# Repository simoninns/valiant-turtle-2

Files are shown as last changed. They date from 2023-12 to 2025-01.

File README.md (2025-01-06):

# Valiant Turtle 2
The Valiant Turtle 2 is a modern re-creation of the Valiant Turtle robot from the 1980s.  The project is fully open-hardware and open-software and is designed to be 3D printed and constructed from widely available parts.

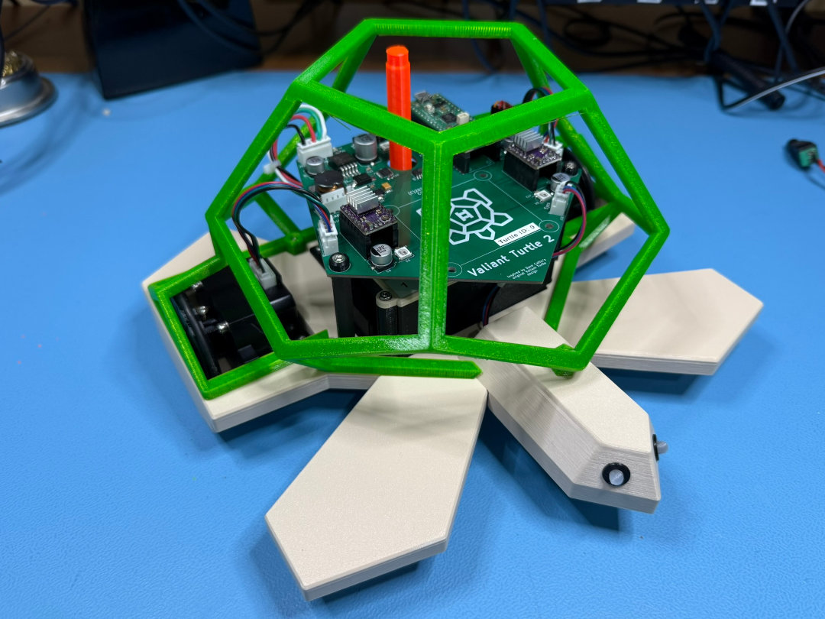
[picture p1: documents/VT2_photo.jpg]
Valiant Turtle 2


Please see the project Wiki for details of the project and for access to the project documentation.

## Project status
This project is at first release.  Please read the wiki and see YouTube for consruction videos (detailed in the wiki also).

## Author
Valiant Turtle 2 is designed and maintained by Simon Inns.

## Software License (GPLv3)

    Valiant Turtle 2 is free software: you can redistribute it and/or modify
    it under the terms of the GNU General Public License as published by
    the Free Software Foundation, either version 3 of the License, or
    (at your option) any later version.

    Valiant Turtle 2 is distributed in the hope that it will be useful,
    but WITHOUT ANY WARRANTY; without even the implied warranty of
    MERCHANTABILITY or FITNESS FOR A PARTICULAR PURPOSE.  See the
    GNU General Public License for more details.

    You should have received a copy of the GNU General Public License
    along with this program.  If not, see <http://www.gnu.org/licenses/>.

## Hardware License (Creative Commons BY-SA 4.0)
Please see the following link for details: https://creativecommons.org/licenses/by-sa/4.0/

You are free to:

Share - copy and redistribute the material in any medium or format
Adapt - remix, transform, and build upon the material
for any purpose, even commercially.

This license is acceptable for Free Cultural Works.

The licensor cannot revoke these freedoms as long as you follow the license terms.

Under the following terms:

Attribution - You must give appropriate credit, provide a link to the license, and indicate if changes were made. You may do so in any reasonable manner, but not in any way that suggests the licensor endorses you or your use.

ShareAlike - If you remix, transform, or build upon the material, you must distribute your contributions under the same license as the original.

No additional restrictions - You may not apply legal terms or technological measures that legally restrict others from doing anything the license permits.

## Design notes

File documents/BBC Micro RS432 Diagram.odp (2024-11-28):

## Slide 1

BBC Micro RS432 DTE

(Top)

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
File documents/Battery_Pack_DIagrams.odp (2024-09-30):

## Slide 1

18650

+

18650

+

18650

+

18650

+

BMS

B3

B2

B1

B+

B-

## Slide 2

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
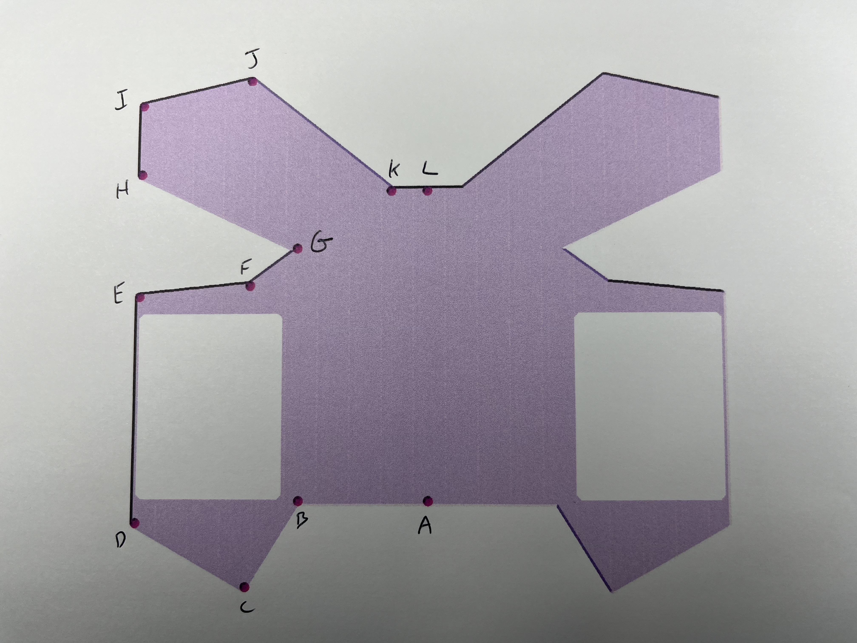
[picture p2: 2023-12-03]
openscad/robot/doc/body_points.jpg

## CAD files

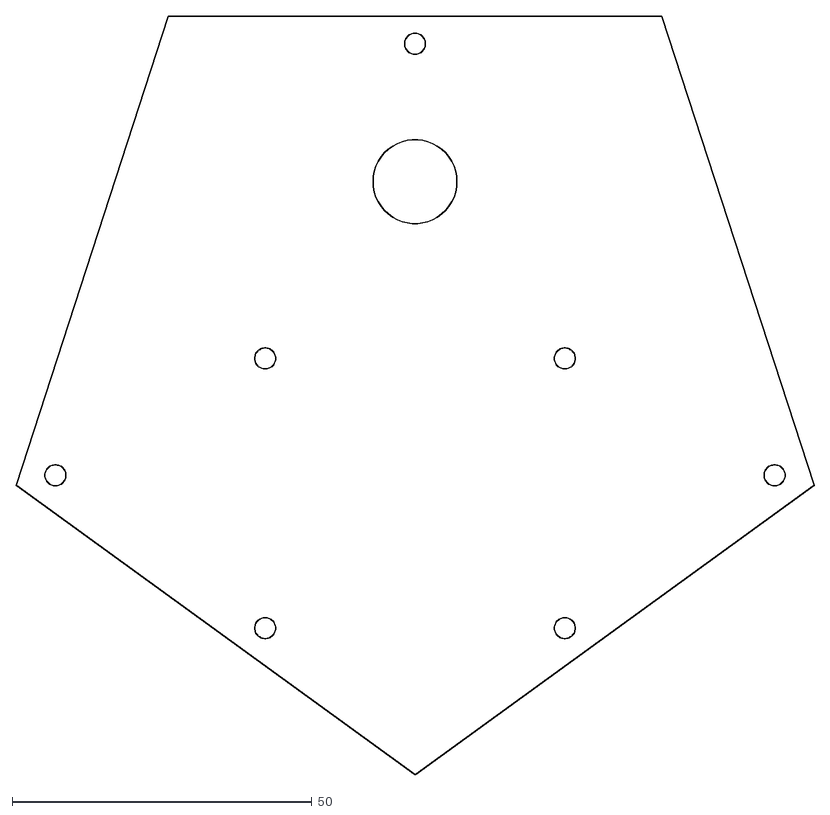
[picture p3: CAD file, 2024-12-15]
openscad/robot/dxf/main_pcb.dxf
133.1 x 126.6

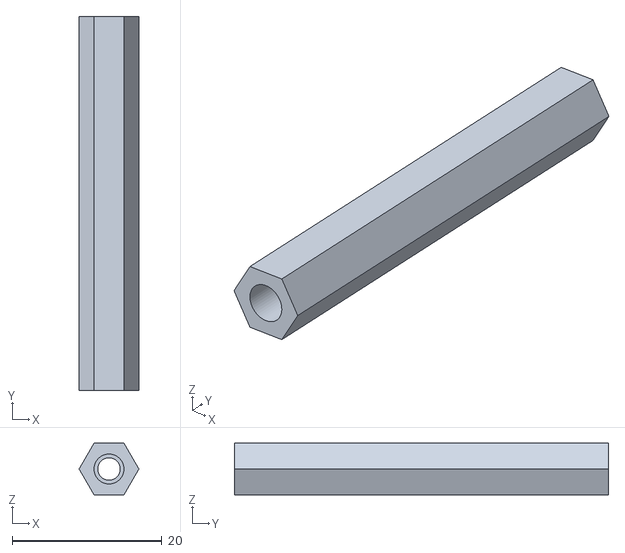
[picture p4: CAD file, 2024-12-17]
openscad/robot/stl/main_pcb_mounts_front.stl
8.00 x 50.0 x 6.93

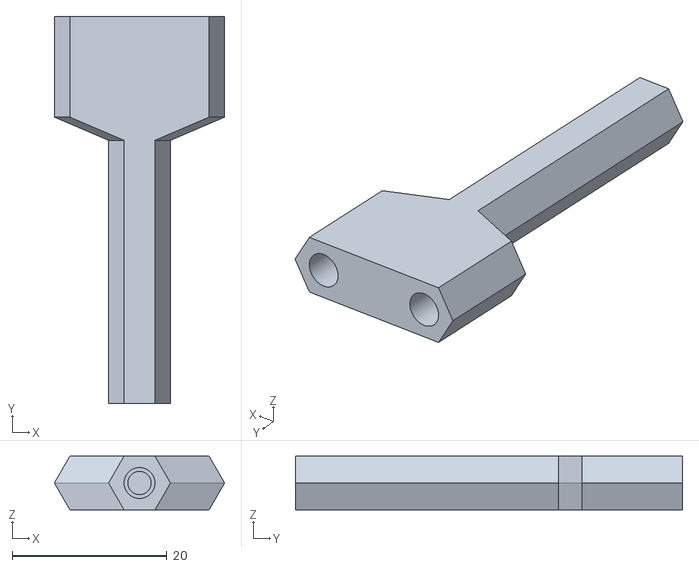
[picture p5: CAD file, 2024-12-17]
openscad/robot/stl/main_pcb_mounts_back.stl
22.0 x 50.0 x 6.93

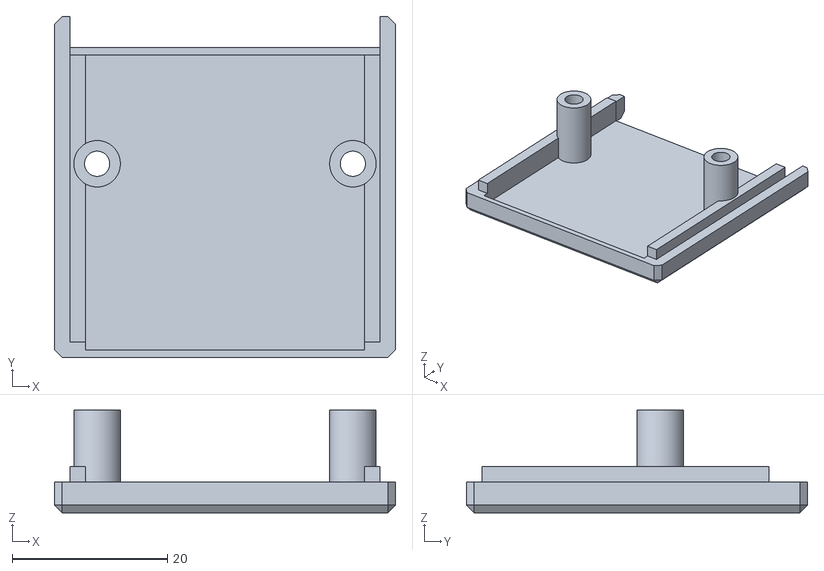
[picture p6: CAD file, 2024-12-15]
openscad/acorn_userport_adapter/stl/case_top.stl
44.0 x 44.0 x 13.2

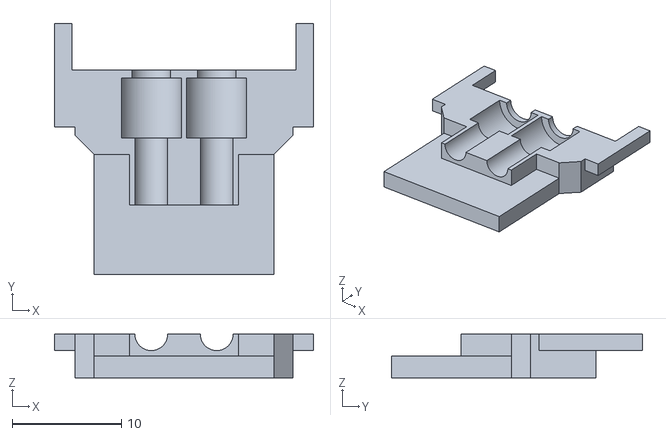
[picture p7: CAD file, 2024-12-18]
openscad/charger/stl/connector_front.stl
23.8 x 23.0 x 4.00

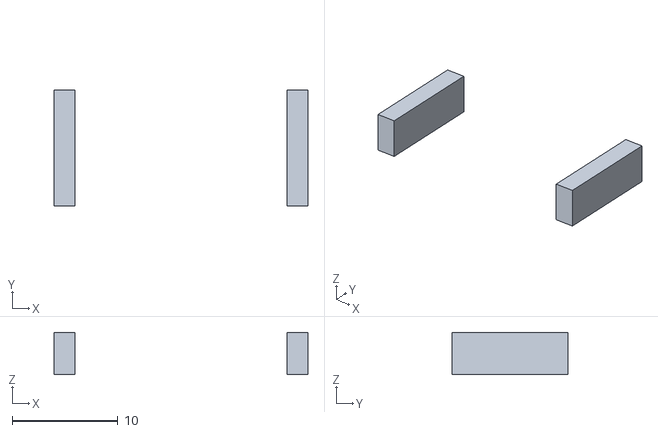
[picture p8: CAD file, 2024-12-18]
openscad/charger/stl_support_enforcers/connector_back_support_enforcer.stl
24.0 x 11.0 x 4.00

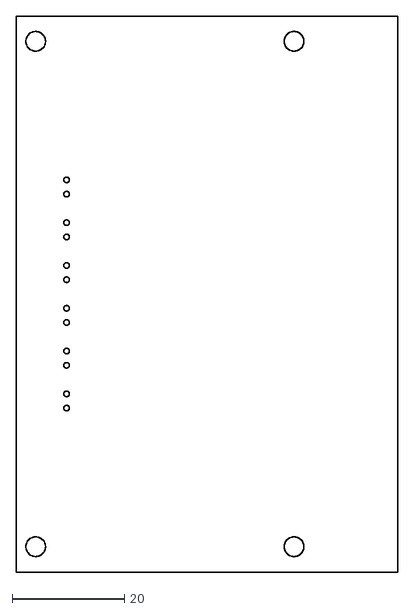
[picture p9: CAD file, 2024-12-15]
openscad/communicator/dxf/pcb.dxf
68.0 x 99.0

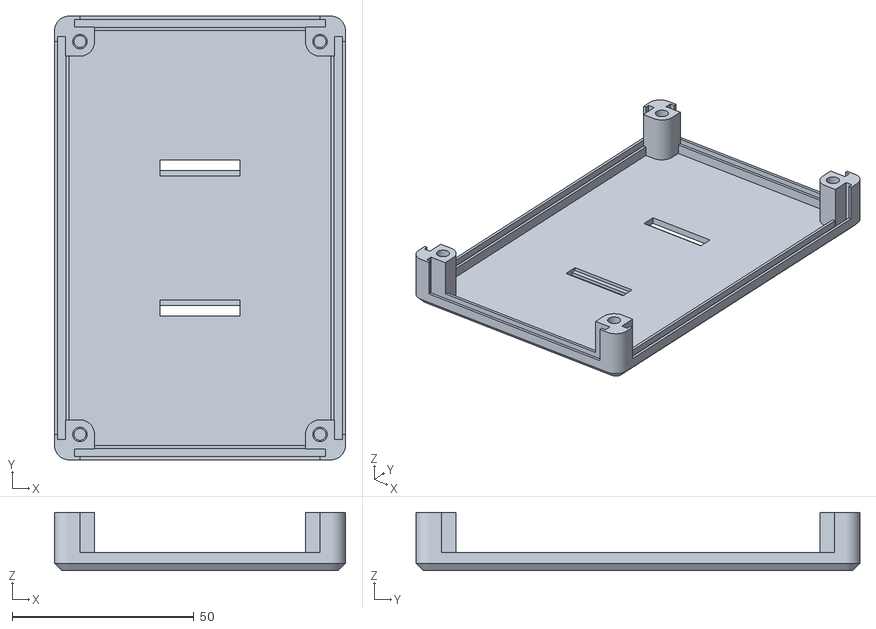
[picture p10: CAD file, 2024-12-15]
openscad/communicator/stl/case_top.stl
80.0 x 122.0 x 16.0

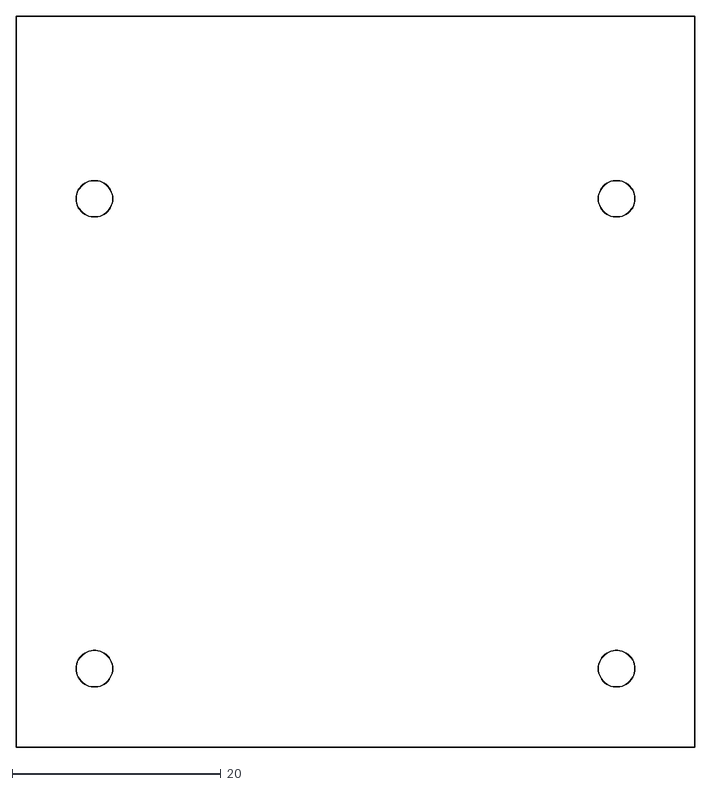
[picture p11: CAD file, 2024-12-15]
openscad/robot/dxf/aux_pcb.dxf
65.0 x 70.0

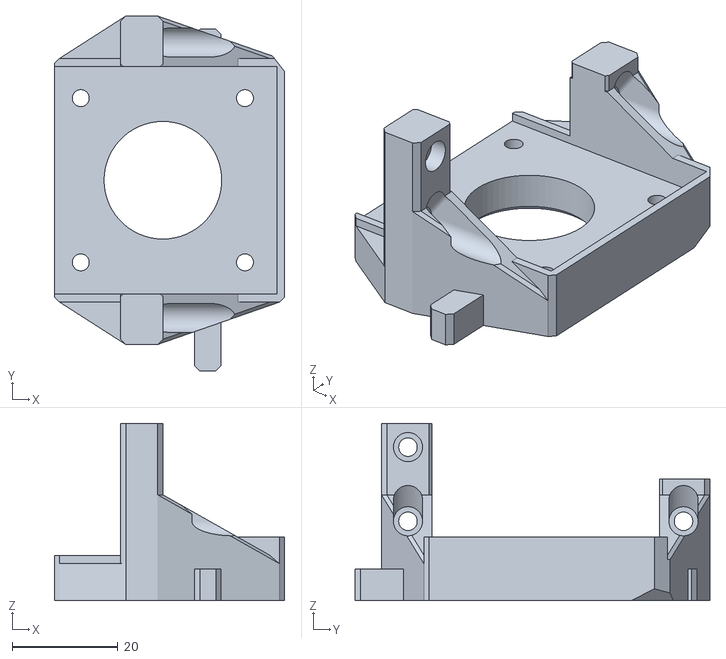
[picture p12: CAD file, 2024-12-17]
openscad/robot/stl/motor_mount_right.stl
43.5 x 67.0 x 33.5

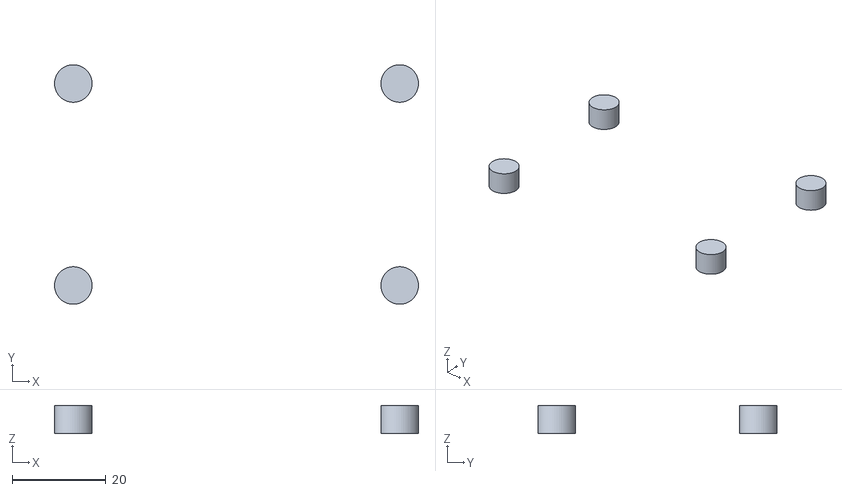
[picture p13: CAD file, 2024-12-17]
openscad/robot/stl_support_enforcers/body_right_support_enforcer.stl
77.5 x 51.0 x 6.00

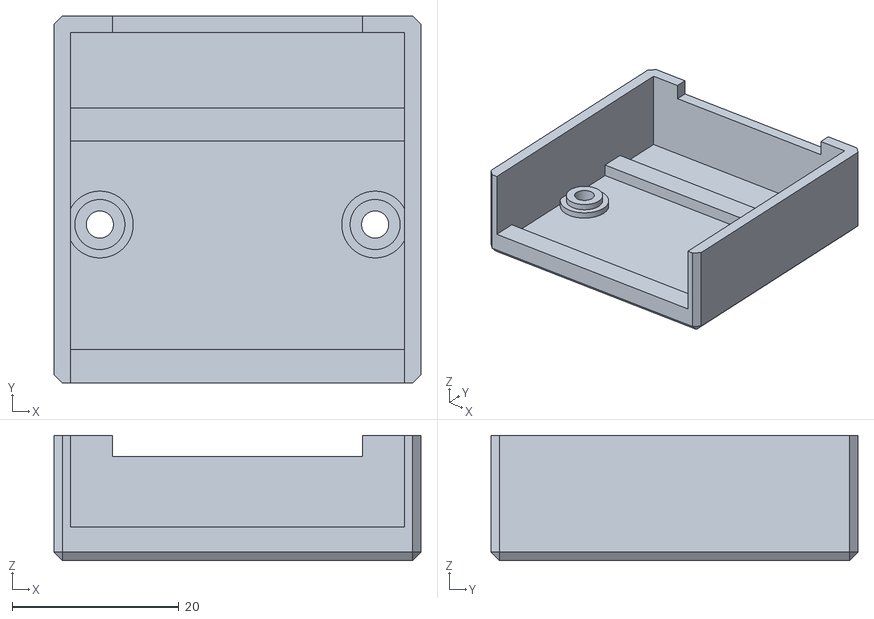
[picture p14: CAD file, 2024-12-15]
openscad/acorn_userport_adapter/stl/case_bottom.stl
44.0 x 44.0 x 15.0

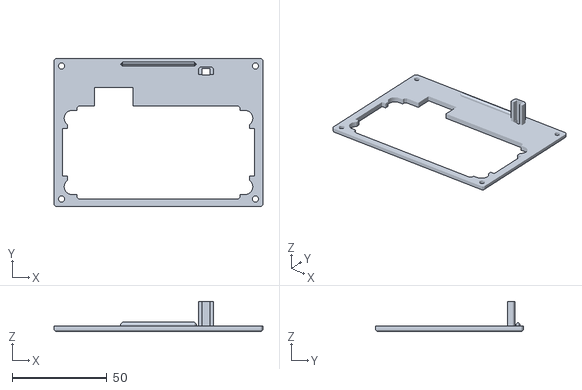
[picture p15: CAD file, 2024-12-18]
openscad/charger/stl/lid.stl
110.0 x 78.0 x 16.0

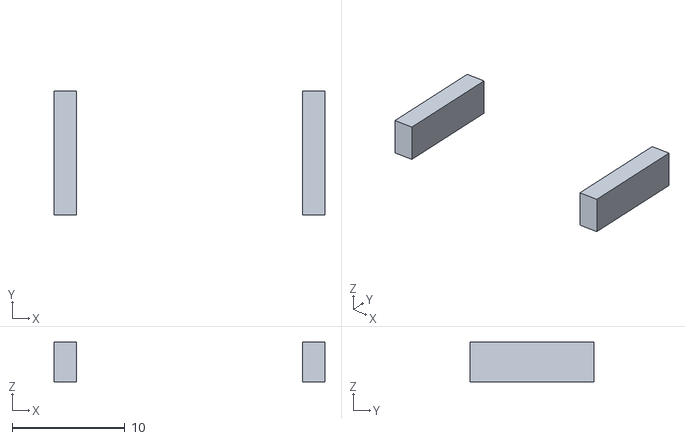
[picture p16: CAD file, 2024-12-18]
openscad/charger/stl_support_enforcers/connector_front_support_enforcer.stl
24.0 x 11.0 x 3.50

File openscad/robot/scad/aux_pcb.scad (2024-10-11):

/************************************************************************

    aux_pcb.scad
    
    Valiant Turtle 2
    Copyright (C) 2024 Simon Inns
    
    This is free software: you can redistribute it and/or modify
    it under the terms of the GNU General Public License as published by
    the Free Software Foundation, either version 3 of the License, or
    (at your option) any later version.
    
    This program is distributed in the hope that it will be useful,
    but WITHOUT ANY WARRANTY; without even the implied warranty of
    MERCHANTABILITY or FITNESS FOR A PARTICULAR PURPOSE.  See the
    GNU General Public License for more details.
    
    You should have received a copy of the GNU General Public License
    along with this program.  If not, see <http://www.gnu.org/licenses/>.
    
    Email: simon.inns@gmail.com
    
************************************************************************/

include <BOSL/constants.scad>
use <BOSL/transforms.scad>
use <BOSL/shapes.scad>

include <main_pcb.scad>

// Screw holes for the aux board
module aux_screws()
{
    move([0,0,0]) {
        move([+(50/2),+(45/2),0]) cyl(h=10, d=3.5);
        move([-(50/2),+(45/2),0]) cyl(h=10, d=3.5);
        move([+(50/2),-(45/2),0]) cyl(h=10, d=3.5);
        move([-(50/2),-(45/2),0]) cyl(h=10, d=3.5);
    }
}

// The aux PCB is to allow easy additions to the turtle without
// having to redesign the main control board.
module aux_pcb() 
{
    move([0,-23,1.5+20]) {
        difference() {
             color([0.0,0.6,0.0,1]) move([0,5,0]) cuboid([55+10,50+20,1.5]);
            aux_screws();
        }
    }
}

module aux_pcb_mount_pillar()
{
    difference() {
        // Pillar
        cyl(h=20, d=8, $fn=6);

        // Threaded insert slot
        move([0,0,14 - 6]) xrot(180) cyl(h=8,d=4);
        move([0,0,-14 + 6]) xrot(180) cyl(h=8,d=4);
        move([0,0,0]) xrot(180) cyl(h=28,d=3);
    }
}

module aux_pcb_mount()
{
    move([0,0,10.75]) {
        move([+(50/2),+(45/2),0]) aux_pcb_mount_pillar();
        move([-(50/2),+(45/2),0]) aux_pcb_mount_pillar();
        move([+(50/2),-(45/2),0]) aux_pcb_mount_pillar();
        move([-(50/2),-(45/2),0]) aux_pcb_mount_pillar();
    }
}

module aux_pcb_screw_washer()
{
    // Use the same part as the main PCB
    main_pcb_screw_washer();
}

module aux_pcb_screw_washers()
{
    move([0,0,0]) {
        move([+(50/2),+(45/2),0]) aux_pcb_screw_washer();
        move([-(50/2),+(45/2),0]) aux_pcb_screw_washer();
        move([+(50/2),-(45/2),0]) aux_pcb_screw_washer();
        move([-(50/2),-(45/2),0]) aux_pcb_screw_washer();
    }
}

module render_aux_pcb(toPrint)
{
    if (!toPrint) {
        difference() {
            move([0,0,50.75]) aux_pcb();
        }
    } else {
        // This will allow you to render and export a DXF file that
        // can be used as a KiCAD PCB outline...
        projection() {
            aux_pcb();
        }
    }
}

module render_aux_pcb_mount(toPrint)
{
    if (!toPrint) {
            move([0,-23,50.75]) color([0.2,0.2,0.2,1]) aux_pcb_mount();
    } else {
        move([0,0,10]) aux_pcb_mount_pillar();
    }
}

module render_aux_pcb_screw_washer(toPrint)
{
    if (!toPrint) {
        move([0,-23,50.75]) color([0.2,0.2,0.2,1]) {
            move([0,0,24.25]) aux_pcb_screw_washers();
            zflip() move([0,0,2.75]) aux_pcb_screw_washers();
        }
    }
}

module render_aux_pcb_screws(toPrint)
{
    if (!toPrint) {
        // Top screws
        move([0,-23,74.5]) {
            move([+(50/2),+(45/2),0]) m3x10_screw();
            move([-(50/2),+(45/2),0]) m3x10_screw();
            move([+(50/2),-(45/2),0]) m3x10_screw();
            move([-(50/2),-(45/2),0]) m3x10_screw();
        }

        // Bottom screws
        move([0,-23,48.5]) {
            move([+(50/2),+(45/2),0]) xrot(180) m3x10_screw();
            move([-(50/2),+(45/2),0]) xrot(180) m3x10_screw();
            move([+(50/2),-(45/2),0]) xrot(180) m3x10_screw();
            move([-(50/2),-(45/2),0]) xrot(180) m3x10_screw();
        }
    }
}

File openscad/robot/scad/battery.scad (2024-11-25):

/************************************************************************

    battery.scad
    
    Valiant Turtle 2
    Copyright (C) 2024 Simon Inns
    
    This is free software: you can redistribute it and/or modify
    it under the terms of the GNU General Public License as published by
    the Free Software Foundation, either version 3 of the License, or
    (at your option) any later version.
    
    This program is distributed in the hope that it will be useful,
    but WITHOUT ANY WARRANTY; without even the implied warranty of
    MERCHANTABILITY or FITNESS FOR A PARTICULAR PURPOSE.  See the
    GNU General Public License for more details.
    
    You should have received a copy of the GNU General Public License
    along with this program.  If not, see <http://www.gnu.org/licenses/>.
    
    Email: simon.inns@gmail.com
    
************************************************************************/

include <BOSL/constants.scad>
use <BOSL/transforms.scad>
use <BOSL/shapes.scad>

// Non-printable parts ------------------------------------------------------------------

module battery18650_protected()
{
    // 18650 Battery with protection circuit
    difference() {
        cyl(h=69, d=18.5);
        move([0,0,(69/2)]) cyl(h=0.5, d=13);
        move([0,0,-(69/2)]) cyl(h=0.5, d=13);
    }
    
    move([0,0,(69/2)+0.25]) cyl(h=1, d=5);
}

module battery18650()
{
    // 18650 Battery without protection circuit
    difference() {
        cyl(h=65, d=18.5);
        move([0,0,(65/2)]) cyl(h=0.5, d=13);
        move([0,0,-(65/2)]) cyl(h=0.5, d=13);
    }
    
    move([0,0,(65/2)+0.25]) cyl(h=1, d=5);
}

module batteries()
{
    move([0,-2,0]) {
        move([19,10.25,1]) battery18650();
        move([19,-10.25,-1]) xrot(180) battery18650();

        move([-5.5,10.25,-1]) xrot(180) battery18650();
        move([-5.5,-10.25,1]) battery18650();
    }
}

module bullet_4mm_female()
{
    move([0,0,12.25/2]) difference() {
        union() {
            move([0,0,0]) cyl(h=12.25, d=4.25);
            move([0,0,-4.5-0.125]) cyl(h=3, d=4.75);
            move([0,0,-2.5 - 0.125 + 0.75 - 0.125]) cyl(h=0.75, d=4.75);
        }

        move([0,0,9.5 - 6]) cyl(h=7, d=3.5);
        move([0,0,-9.5+4]) cyl(h=7, d=3.5);
    }
}

module bms_pcb()
{
    difference() {
        union() {
            color([0,0.6,0,1]) cuboid([34,34,1.25], fillet=5, edges=EDGES_Z_ALL);

            // Pads
            color([0.8,0.8,0.0,1]) move([0,0,1]) {
                move([0,-15.5,0]) {
                    move([-9,0,0]) cuboid([6,3,1]); // B1
                    move([0,0,0]) cuboid([6,3,1]);  // B2
                    move([+9,0,0]) cuboid([6,3,1]);  // B3
                }

                move([-15.5,0,0]) cuboid([3,6,1]); // B-
                move([+15.5,0,0]) cuboid([3,6,1]); // B+

                move([0,14,-0.25]) {
                    move([-1.5 - 1.5,0,0]) cuboid([3,6,0.5], fillet=1.5, edges=EDGES_Z_ALL); // B1
                    move([+1.5 + 1.5,0,0]) cuboid([3,6,0.5], fillet=1.5, edges=EDGES_Z_ALL);  // B3
                }
            }
        }

        // Wire holes
        move([0,14,0]) {
            move([-1.5 - 1.5,0,0]) cyl(h=4,d=1);
            move([+1.5 + 1.5,0,0]) cyl(h=4,d=1);
        }
    }
}

// BMS PCB mock-up
module battery_pack_bms_pcb()
{
    move([0,-12.5,-8.5-8]) yrot(180) bms_pcb();
}

// Printable parts ----------------------------------------------------------------------

module battery_pack_clip()
{
    move([41.5,0,-15]) { 
        difference() {
            union() {
                move([3.5,0,+2.5]) cuboid([9, 24,35]);
                move([-1,-12,20]) right_triangle([9, 24, 9]);

                // Tab
                move([8.5,0,-13]) cuboid([3,18,4], chamfer=1, edges=EDGES_Z_ALL+EDGES_RIGHT);

                // Clip
                move([8,-9,6]) {
                    difference() {
                        right_triangle([3, 18, 3]);
                        move([4,9,0]) cuboid([3.5,20,3]);
                    }
                }
            }

            move([-2,0,-2]) union() {
                move([3.5,0,+2.5]) cuboid([9, 18+2,37.1]);
                move([-1,-10,21]) right_triangle([9, 18+2, 9]);
            }

            // Cut-outs to form side protectors
            move([+4,-9.5,9]) cuboid([24, 1,50]);
            move([+4,+9.5,9]) cuboid([24, 1,50]);
        }
    }
}

module bullet_connector_female_mask()
{
    move([0,0,9]) cyl(h=9,d=4.5);
    move([0,0,-0.5]) cyl(h=1,d=4);
    move([0,0,2.25]) cyl(h=5,d=5.5);
}

module battery_pack_screw_columns()
{
    // Screw columns
    move([45.5,18,-4]) {
        difference() {
            hull() {
                cyl(h=52,d=8);
                move([-4,0,0]) cuboid([1,8,52]); 
            }

            // Threaded insert
            cyl(h=64,d=3.25);
            move([0,0,+(34 - 10)]) cyl(h=8,d=4);
            move([0,0,-(34 - 10)]) cyl(h=8,d=4);
        }
    }

    move([45.5,-18,-4]) {
        difference() {
            hull() {
                cyl(h=52,d=8);
                move([-4,0,0]) cuboid([1,8,52]); 
            }

            // Threaded insert
            cyl(h=64,d=3.25);
            move([0,0,+(34 - 10)]) cyl(h=8,d=4);
            move([0,0,-(34 - 10)]) cyl(h=8,d=4);
        }
    }

    move([-45.5,18,-4]) {
        difference() {
            hull() {
                cyl(h=52,d=8);
                move([+4,0,0]) cuboid([1,8,52]); 
            }

            // Threaded insert
            cyl(h=64,d=3.25);
            move([0,0,+(34 - 10)]) cyl(h=8,d=4);
            move([0,0,-(34 - 10)]) cyl(h=8,d=4);
        }
    }

    move([-45.5,-18,-4]) {
        difference() {
            hull() {
                cyl(h=52,d=8);
                move([+4,0,0]) cuboid([1,8,52]); 
            }

            // Threaded insert
            cyl(h=64,d=3.25);
            move([0,0,+(34 - 10)]) cyl(h=8,d=4);
            move([0,0,-(34 - 10)]) cyl(h=8,d=4);
        }
    }
}

module battery_pack()
{
    difference() {
        move([0,-12.5,10]) {
            difference() {
                union() {
                    cuboid([86-0.5,49-0.5,60 -16], chamfer=1, edges=EDGES_Z_ALL);
                    move([0,0,-21.5]) cuboid([88,49-0.5,17], chamfer=1, edges=EDGES_Z_ALL);

                    // Battery connector
                    move([-23.5,27,-20.5]) move([0,-0.5,2.25]) cuboid([14,5,23.5]);
                }
                cuboid([81,44,64], chamfer=1, edges=EDGES_Z_ALL);

                // Battery connector
                move([-23.5 - 3,29,-22 + 3]) bullet_connector_female_mask();
                move([-23.5 + 3,29,-22 + 3]) bullet_connector_female_mask();

                // Cable gap
                move([-23.5 - 3,25,-27 + 0]) cuboid([4,10,8]);
                move([-23.5 + 3,25,-27 + 0]) cuboid([4,10,8]);
                move([-23.5 - 3,29,-24.5 + 3]) cyl(h=4,d=4);
                move([-23.5 + 3,29,-24.5 + 3]) cyl(h=4,d=4);

                // Clip slots
                move([-33.5,0,-17.25]) { 
                    move([1,23,0]) cuboid([2.5,9,21.5]);
                    move([19,23,0]) cuboid([2.5,9,21.5]);

                    // Angle the top of the slots for better printing
                    move([1,23,10.75]) yrot(45) cuboid([1.75,9,1.75]);
                    move([19,23,10.75]) yrot(45) cuboid([1.75,9,1.75]);
                    move([0.25 + 0.125,21,10.75]) yrot(45) cuboid([2.75 - 0.125,4,2.75 - 0.125]);
                    move([19.25 + 0.25 + 0.125,21,10.75]) yrot(45) cuboid([2.75 - 0.125,4,2.75 - 0.125]);

                    // Clip recess
                    move([-0.5,22,0]) cuboid([2,2,21.5]);
                    move([20.5,22,0]) cuboid([2,2,21.5]);
                }

                // Lower screw clearance
                move([45.5,18,-(34 - 6)]) cyl(h=8,d=4);
                move([-45.5,18,-(34 - 6)]) cyl(h=8,d=4);
                move([45.5,-18,-(34 - 6)]) cyl(h=8,d=4);
                move([-45.5,-18,-(34 - 6)]) cyl(h=8,d=4);
            }

            // Clip base
            move([-23.5,28,-29]) cuboid([20,12,2]);

            battery_pack_clip();
            xflip() battery_pack_clip();

            battery_pack_screw_columns();
        }

        // Recess for cover lock
        move([-23.5,9.75,-4.5]) cuboid([18.25,2,14.5]);
    }
}

module battery_pack_supports()
{
    move([+50.5,-12.5,-7]) cuboid([6,18,26]);
    move([-50.5,-12.5,-7]) cuboid([6,18,26]);
}

module battery_pack_connector_cover()
{
    move([0,-10.5,-21.5+3]) {
        // Battery connector
        difference() {
            difference() {
                move([-23.5,27.25,11.25]) cuboid([18,9.5,17.5 + 4]);
                move([-23.5,26.75 - 4,10]) cuboid([20,8.5,25]);
            }
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

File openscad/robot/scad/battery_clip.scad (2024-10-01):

/************************************************************************

    battery_clip.scad
    
    Valiant Turtle 2
    Copyright (C) 2024 Simon Inns
    
    This is free software: you can redistribute it and/or modify
    it under the terms of the GNU General Public License as published by
    the Free Software Foundation, either version 3 of the License, or
    (at your option) any later version.
    
    This program is distributed in the hope that it will be useful,
    but WITHOUT ANY WARRANTY; without even the implied warranty of
    MERCHANTABILITY or FITNESS FOR A PARTICULAR PURPOSE.  See the
    GNU General Public License for more details.
    
    You should have received a copy of the GNU General Public License
    along with this program.  If not, see <http://www.gnu.org/licenses/>.
    
    Email: simon.inns@gmail.com
    
************************************************************************/

include <BOSL/constants.scad>
use <BOSL/transforms.scad>
use <BOSL/shapes.scad>

// Battery contact (basic shape)
module battery_contact()
{
    difference() {
        union() {
            // Main body round lower part
            difference() {
                cyl(h=0.3, d=18.5);
                move([0,18.5/2,0]) cuboid([18.5+1,18.5, 1]);
            }

            // Main box rectangular upper part
            move([0,0+7/2,0]) cuboid([18.5,7, 0.3]);

            // Clips
            move([(8.25 - 0.5),6 - 5,0 +0.6]) zrot(180) right_triangle(size=[2,2,1.5], orient=ORIENT_X, center=true);
            move([-(8.25 - 0.5),6 - 5,0 +0.6]) zrot(180) right_triangle(size=[2,2,1.5], orient=ORIENT_X, center=true);

            // Soldering tag
            move([0,-14,0]) cuboid([5,1, 0.3]);
            move([0,-13.75+0.1,-0.5]) cuboid([5,0.3, 1.25]);

            move([0,-16.75,-1.25]) cuboid([5,6.5, 0.3]);
            move([0,-3,-1.25]) cyl(h=0.3, d=5);
        }

        move([0,-3,-1.25]) cyl(h=2, d=2.25);
    }
}

module battery_contact_negative()
{
    difference() {
        battery_contact();
        move([0,-1,0]) cyl(h=1,d=3);
    }
    
    // Spring 12mm high, 6mm,
    move([0,-1,6]) cyl(h=12, d=6); 

}

module battery_contact_positive()
{
    difference() {
        battery_contact();
        move([0,-1,0]) cyl(h=1,d=10);
    }

    move([0,-1,0]) {
        difference() {
            hull() {
                move([0,0,2]) cyl(h=0.3, d=6);
                move([0,0,0]) cyl(h=0.3,d=10);
            }

            move([0,0,-0.3]) hull() {
                move([0,0,2]) cyl(h=0.3, d=6);
                move([0,0,0]) cyl(h=0.3,d=10);
            }
        }
    }
}


module battery_contact_mask()
{
    cuboid([19,16,0.5]);

    // Centre clearance
    move([0,1,-2]) cuboid([11.5,14,4]);

    // Back centre clearance
    move([0,-3,2]) cuboid([5.5,10,4]);
    move([0,2,2]) zrot(45) cuboid([4,4,4]);
    move([0,-6,2]) cuboid([5.5,14,2]);

    // Tab clearance
    move([0,-10,0]) cuboid([5.5,16,0.5]);

    // Fastening clip channels
    move([(8.25 - 0.5),0.75,-0.75]) cuboid([2.5,3,1.25]);
    move([-(8.25 - 0.5),0.75,-0.75]) cuboid([2.5,3,1.25]);

    move([(8.25 - 0.5),5,-0.5]) cuboid([2.5,6,0.75]);
    move([-(8.25 - 0.5),5,-0.5]) cuboid([2.5,6,0.75]);
}


// 18650 x2 Battery clip
module battery_clip_body()
{
    difference() {
        union() {
            move([0,0,3.5+3]) cuboid([43,76,13], chamfer=0.5);
            move([0,+36.25,7+4]) cuboid([43,3.5,12], chamfer=0.5);
            move([0,-36.25,7+4]) cuboid([43,3.5,12], chamfer=0.5);
        }

        // Battery recesses
        move([-10.25,0,8.5]) ycyl(h=69,d=19);
        move([+10.25,0,8.5]) ycyl(h=69,d=19);

        // Screw recesses
        move([0,-(55.5/2),7.5]) cyl(h=13,d1=8, d2=12);
        move([0,+(55.5/2),7.5]) cyl(h=13,d1=8, d2=12);

        // Screw holes
        move([0,-(55.5/2),0]) cyl(h=8,d=3.5);
        move([0,+(55.5/2),0]) cyl(h=8,d=3.5);

        // Positive markers
        move([17,38.25,8]) {
            cuboid([5,1,1]);
            cuboid([1,1,5]);
        }

        move([-17,-38.25,8]) {
            cuboid([5,1,1]);
            cuboid([1,1,5]);
        }

        // Negative markers
        move([-17,38.25,8]) {
            cuboid([5,1,1]);
        }

        move([+17,-38.25,8]) {
            cuboid([5,1,1]);
        }

        // Orientation tab
        move([-18.75 + 1.5,-38.25 + 2,0]) cyl(h=1.1,d1=3, d2=2);

        // Side cut-outs to help get the batteries in and out
        move([0,18,11]) cuboid([48,22,9], chamfer=2);
        move([0,-18,11]) cuboid([48,22,9], chamfer=2);

        // Wiring gully
        move([0,39.5,6.5]) cuboid([20,4,4], chamfer=1);
        move([0,-39.5,6.5]) cuboid([20,4,4], chamfer=1);
    }
}

module battery_clip()
{
    difference() {
        battery_clip_body();

        xrot(90) {
            move([10.25,9.01,36.25]) battery_contact_mask();
            move([-10.25,9.01,36.25]) battery_contact_mask();
        }

        xrot(90) {
            move([10.25,9.01,-36.25]) yrot(180) battery_contact_mask();
            move([-10.25,9.01,-36.25]) yrot(180) battery_contact_mask();
        }
    }
}

module battery_clips()
{
    move([-1,0,0]) {
        xrot(-90) zrot(180) {
            move([10.25,9,-36.25]) battery_contact_positive();
            move([-10.25,9,-36.25]) battery_contact_negative();
        }

        xrot(90) zrot(0) {
            move([10.25,9,-36.25]) battery_contact_positive();
            move([-10.25,9,-36.25]) battery_contact_negative();
        }
    }
}

module render_battery_clip(toPrint)
{
    if (!toPrint) {
        color([0.2, 0.2, 0.2]) move([0,-12.5,9]) {
            move([0,-2.5,0]) yrot(90) xrot(90) zrot(180) battery_clip();
            move([0,+2.5,0]) yrot(90) xrot(-90) zrot(180) battery_clip();
        }
    } else {
        battery_clip();
    }
}

module render_battery_clip_contacts(toPrint)
{
    if (!toPrint) {
        color([0.8, 0.8, 0.8]) move([0,-12.5,10]) {
            move([0,-2.5,0]) yrot(90) xrot(90) zrot(180) battery_clips();
            move([0,+2.5,0]) yrot(90) xrot(-90) zrot(180) battery_clips();
        }
    }
}

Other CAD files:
openscad/communicator/stl/case_base.stl
openscad/robot/stl/head.stl
openscad/robot/stl_support_enforcers/battery_pack_lower_cover_support_enforcer.stl
openscad/acorn_userport_adapter/stl/support_enforcer.stl
openscad/robot/scad/body.scad
openscad/acorn_userport_adapter/scad/case.scad
openscad/acorn_userport_adapter/scad/main.scad
openscad/charger/scad/base.scad
openscad/charger/scad/battery_cutout.scad
openscad/charger/scad/bullet_connector.scad
openscad/charger/scad/connector.scad
openscad/charger/scad/lid.scad
openscad/charger/scad/light_pipe.scad
openscad/charger/scad/main.scad
openscad/charger/scad/pcb.scad
openscad/charger/scad/screws.scad
openscad/charger/stl/base.stl
openscad/charger/stl/connector_back.stl
openscad/charger/stl/light_pipe.stl
openscad/charger/stl_support_enforcers/charger_lid_support_enforcers.stl
openscad/communicator/scad/case.scad
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

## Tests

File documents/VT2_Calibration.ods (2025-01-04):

Valiant Turtle 2 – Calibration calculations
Linear calibration:
 | Diameter | 55.53 | mm
 | Circumference | 174.452640053841 | mm
 | Expected distance | 200 | mm
 | Number of rotations | 1.1464429540205 | rotations
 | Error | 0 | mm
 |  | .
 | Observed distance | 200 | mm
 | Observed diameter | 55.53
 | Difference | 0 | mm
 | Calibration setting | 0 | um
Rotational calibration:
 | Wheel diameter (observed) | 55.53 | mm
 | Circumference | 174.452640053841 | mm
 | Axel distance | 224 | mm
 | Turning circumference | 703.716754404114 | mm
 | Expected degrees of rotation | 1800 | degrees
 | Expected distance | 3518.58377202057
 | Number of rotations | 20.1692778678192
 | Error | -14 | degrees | (negative if turn is short)
 | Observed degrees of rotation | 1814 | degrees
 | Observed axel distance | 222.271223814774 | mm
 | Difference | -1.72877618522591 | mm
 | Calibration setting | 1729 | um

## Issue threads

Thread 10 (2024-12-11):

Make a better shell design for the robot

simoninns, 2024-12-11:
The shell has a number of issues (not least being a little too hard-coded in openscad).

A design that allows for transparent materials, mounting additional modules on the shell and easier printing, should be considered.

simoninns, 2024-12-15:
Fixed

Closed 2024-12-15.

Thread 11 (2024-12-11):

Add calibration sheet as PDF

simoninns, 2024-12-11:
The calibration sheet is only available as an Inkscape SVG at the moment - a PDF would be more useful for most people

simoninns, 2024-12-19:
Fixed

Closed 2024-12-19.

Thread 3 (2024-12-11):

Include battery monitoring and management

simoninns, 2024-12-11:
Right now you can only read the INA260 values manually.  The robot should be monitoring power and performing some actions when the battery is low.

simoninns, 2025-01-04:
Fixed in latest commit

Closed 2025-01-04.

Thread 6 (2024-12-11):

Prevent the Pico's USB connector from powering the robot

simoninns, 2024-12-11:
If you connect a USB cable to the Pico, the robot's 5V circuitry is powered including the LEDs.  This should be prevented.

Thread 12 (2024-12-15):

Servo horn missing support enforcer

simoninns, 2024-12-15:
The robot servo horn is missing a support enforcer for the main screw recess

simoninns, 2024-12-15:
Fixed

Closed 2024-12-15.

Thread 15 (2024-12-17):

BOMs on the wiki are not updated

simoninns, 2024-12-17:
Update all the BoMs on the wiki according to the current KiCAD board designs

simoninns, 2025-01-06:
Updated mainboard PCB BoM

simoninns, 2025-01-06:
Updated communicator BoM

Closed 2025-01-06.

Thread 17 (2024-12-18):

Charger connector missing support enforcers

simoninns, 2024-12-18:
The front and back charger connector is missing support enforcers (should be the same as the connector on the robot)

simoninns, 2024-12-18:
Fixed

Closed 2024-12-18.

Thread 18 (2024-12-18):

Communicator IR window

simoninns, 2024-12-18:
Missing instruction on how to make this and the materials required.

simoninns, 2025-01-06:
Fixed

Closed 2025-01-06.

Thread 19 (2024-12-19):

Create a python 'turtle'-like module

simoninns, 2024-12-19:
Python has a class for turtle graphics - a similar API could be implemented for controlling the VT2 (as well as dealing with connection via BLE and multiple turtles).

simoninns, 2024-12-19:
This should support a Cartesian coordinate system as well tracking the x,y position of the turtle in millimetres.  Like logo, it could support setpos, setx, sety, +xpos, +ypos, +pos and 'towards' which will turn the turtle to face an x,y position.

simoninns, 2025-01-04:
Fixed in latest commit

Closed 2025-01-04.

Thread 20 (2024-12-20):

Add threaded inserts to the servo holder

simoninns, 2024-12-20:
The 9G pen servo is held in place with the screws that generally come with them - directly into the plastic part.

It would be better if M2 or M2.5 bolts were used with threaded inserts in the plastic parts.

simoninns, 2024-12-20:
I measured this and there simply isn't space to do this - the clearance to the side of the servo is too small

Closed 2024-12-20.

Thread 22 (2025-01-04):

Robot firmware should use micrometers internally not millimetres

simoninns, 2025-01-04:
Millimetre accuracy is not good enough.  Convert the robot firmware to use mm on the command interface, but only micrometers internally

simoninns, 2025-01-05:
Fixed in latest commit

Closed 2025-01-05.

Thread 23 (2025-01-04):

Pen holder through PCB

simoninns, 2025-01-04:
It might be possible to extend the pen-holder through the PCB (so you can tighten and loosen it from above).  If so, implement.

simoninns, 2025-01-05:
This would require a redesign of the PCB.  Right now the biggest pen diameter is around 12mm and the PCB aperture is 14mm, so there is no space to get the threading through.

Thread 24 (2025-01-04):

Acornsoft Logo extension SCREEN command implementation

simoninns, 2025-01-04:
The SCREEN command should be able to ignore VT2 errors in the case that the robot is disconnected from the communicator before the SCREEN command is issued.  You should be able to pop back to screen mode without problems even if the robot has been turned off.

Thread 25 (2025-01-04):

Circle control inaccurate in firmware

simoninns, 2025-01-04:
The circle firmware commands do not keep the wheels in sync, so the circle command has a tendency to draw curves towards the start and end of the movement (which causes a loss of tracking accuracy).

simoninns, 2025-01-05:
Found a bug in diffdrive where the axel distance calibration was not being correctly applied.  Also changed diffdrive from millimetres to micrometres.  Probably needs a little more attention though.

simoninns, 2025-01-05:
Fixed in latest commit

Closed 2025-01-05.

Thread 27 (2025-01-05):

Robot firmware motor status LEDs

simoninns, 2025-01-05:
When running calitest2 it looks like the motor status LEDs are not correctly showing the direction of the motors at all times.

simoninns, 2025-01-05:
Fixed

Closed 2025-01-05.

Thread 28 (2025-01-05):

Robot firmware: Diffdrive setposition

simoninns, 2025-01-05:
Since set position is making multiple moves the LEDs are not updating.

This is because diffdrive isn't async so whilst it is waiting for the stepper movement to complete in a while loop, the get motor status call isn't happening (as the async execution is paused until it returns).  Meaning only the final setheading is reflected in the LEDs

Not really a bug, but a bit annoying.

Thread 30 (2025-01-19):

Shell too large for Ender 3

drdpj, 2025-01-19:
Shell STL is too large to print sensibly on something at the smaller end of the print volume scale, like an Ender 3 (220x220x250).

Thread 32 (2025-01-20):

Eye surround tolerance

drdpj, 2025-01-20:
This is going to be subjective with printer - the current 0.1mm difference between light-pipe and eye surround is too tight for mine. Widening the diameter of the hole in the surround to 5.3mm works nicely (0.4mm difference) - perhaps parameterise this?

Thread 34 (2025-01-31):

Bullet Connectors

drdpj, 2025-01-31:
It'd be useful to have a link to some example that fit the model as it stands - I've acquired some that have the same dimensions as the diagram on the wiki, but they really don't fit (it doesn't give any indication of length etc, etc)

simoninns, 2025-01-31:
I've updated the wiki with photos of the actual connectors used and measurements.  Open another issue if the issue persists (stating what's still missing :) )

Closed 2025-01-31.

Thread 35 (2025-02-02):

Bullet connectors

simoninns, 2025-02-02:
It seems there is some variance in the length and shape of the bullet connectors.  To make the model easier to modify it would be good if the grooves that hold the connector in place are only on the 'clip' side (so you only have to reprint the clip if it's wrong).

Also the connector itself should be made parametric to make modifying it easier.

Any examples of other 'shapes' would be useful.

drdpj, 2025-02-02:
https://www.amazon.co.uk/dp/B081TXM3XN

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

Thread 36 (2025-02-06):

Total number of screws and threaded inserts missing from wiki

simoninns, 2025-02-06:
As per the header, count them up and add them to the BoM (it's around 50)

simoninns, 2025-02-06:
It might be possible to use the CAD model to count and report the number required?

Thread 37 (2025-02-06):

Getting started instructions

drdpj, 2025-02-06:
Some instructions about how to load the firmware would probably be useful for many - I've never used micropython before, I used Thonny to upload it to the pico after a bit of googling.

Worth explaining that it connects via bluetooth, and you can do this directly from your PC without the communicator or anything. You don't have to add it as a device, the command line software will handle that.

To run the command line software you need the "bleak" bluetooth library installed. On windows it's just a "pip install bleak".

This should all go in before getting to the calibration.

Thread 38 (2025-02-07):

get_linear_velocity crashes firmware

drdpj, 2025-02-07:
Log output:

[INFO] CommandsRx::get_linear_velocity - Getting linear velocity
Traceback (most recent call last):
  File "<stdin>", line 139, in <module>
  File "main.py", line 203, in <module>
  File "main.py", line 201, in main
  File "asyncio/core.py", line 1, in run
  File "asyncio/core.py", line 1, in run_until_complete
  File "asyncio/core.py", line 1, in run_until_complete
  File "main.py", line 156, in aio_main
  File "asyncio/funcs.py", line 1, in gather
  File "asyncio/core.py", line 1, in run_until_complete
  File "control.py", line 266, in run
TypeError: can't convert float to int

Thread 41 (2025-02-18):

PCB enhancements

simoninns, 2025-02-18:
I was thinking about this a bit and wondering how (if I ever did another version) I would solve the PCB issue...  My conclusion is two-fold... Firstly I would make the PCB rectangular to drop the cost and size down and then I would mount the PCB in a printed pentagon to make it look 'right'.  This would also mean more flexibility around the pen mounting.  Once the board is smaller and cheaper, you could then use PCBA and get someone like JLCPCB to assemble it as well.

Also affects issue #23

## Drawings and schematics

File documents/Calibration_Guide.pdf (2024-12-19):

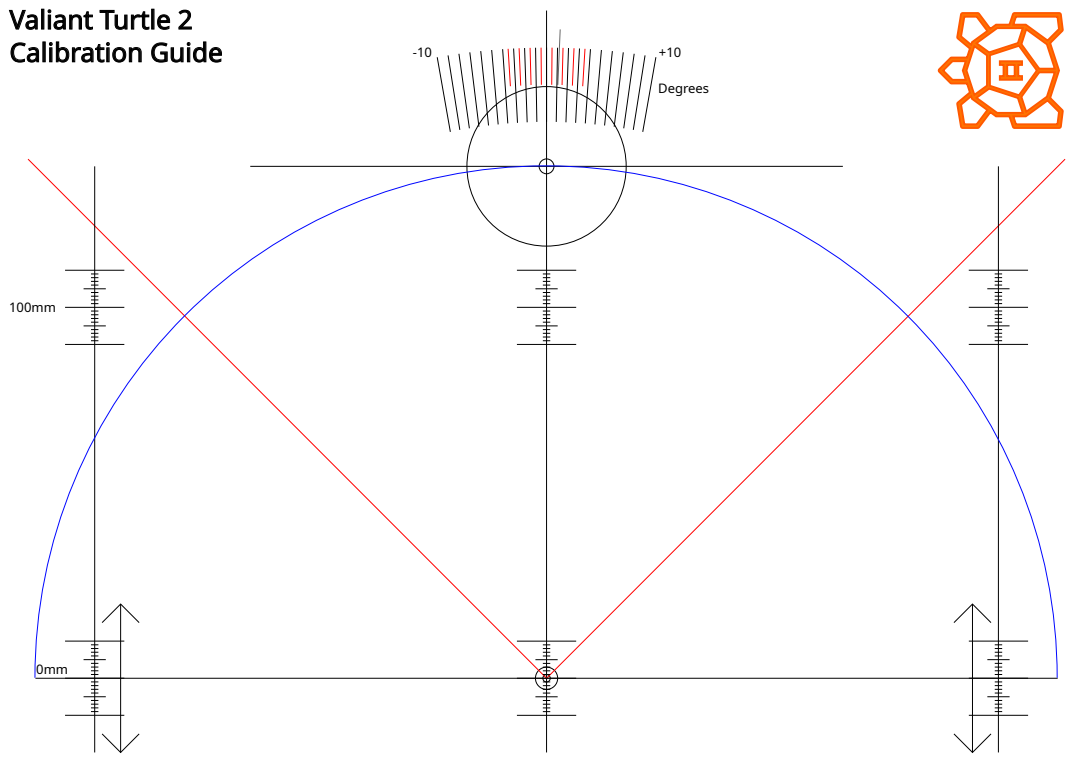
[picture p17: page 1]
Valiant Turtle 2 Calibration Guide; Degrees

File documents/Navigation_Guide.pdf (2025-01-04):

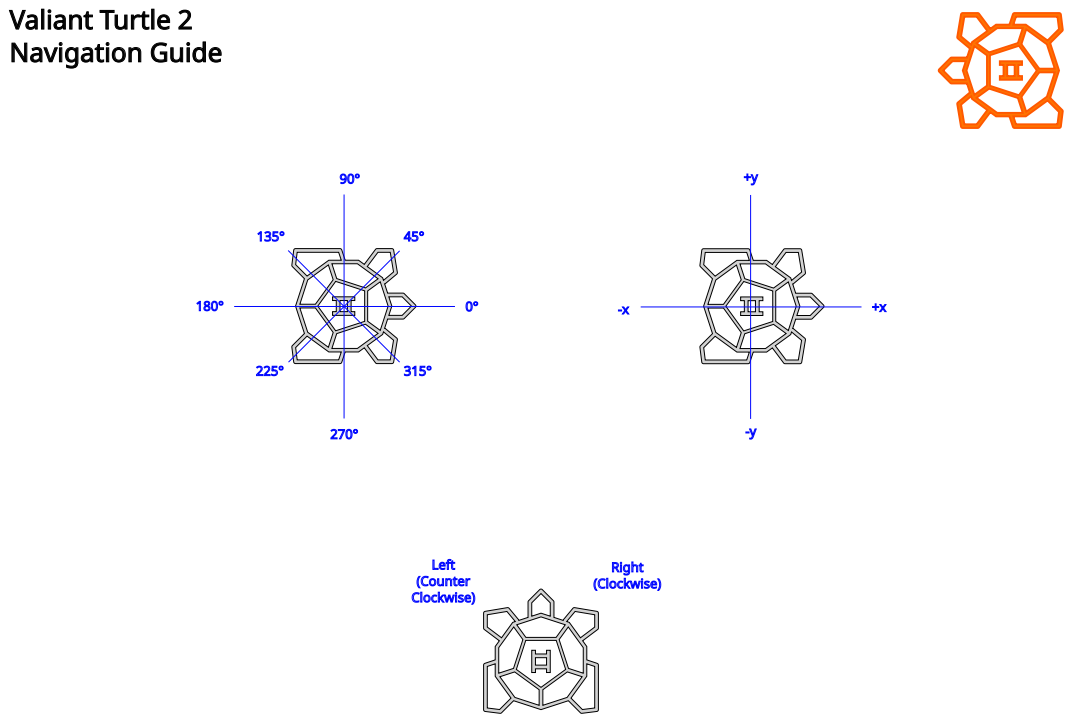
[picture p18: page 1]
Valiant Turtle 2 Navigation Guide

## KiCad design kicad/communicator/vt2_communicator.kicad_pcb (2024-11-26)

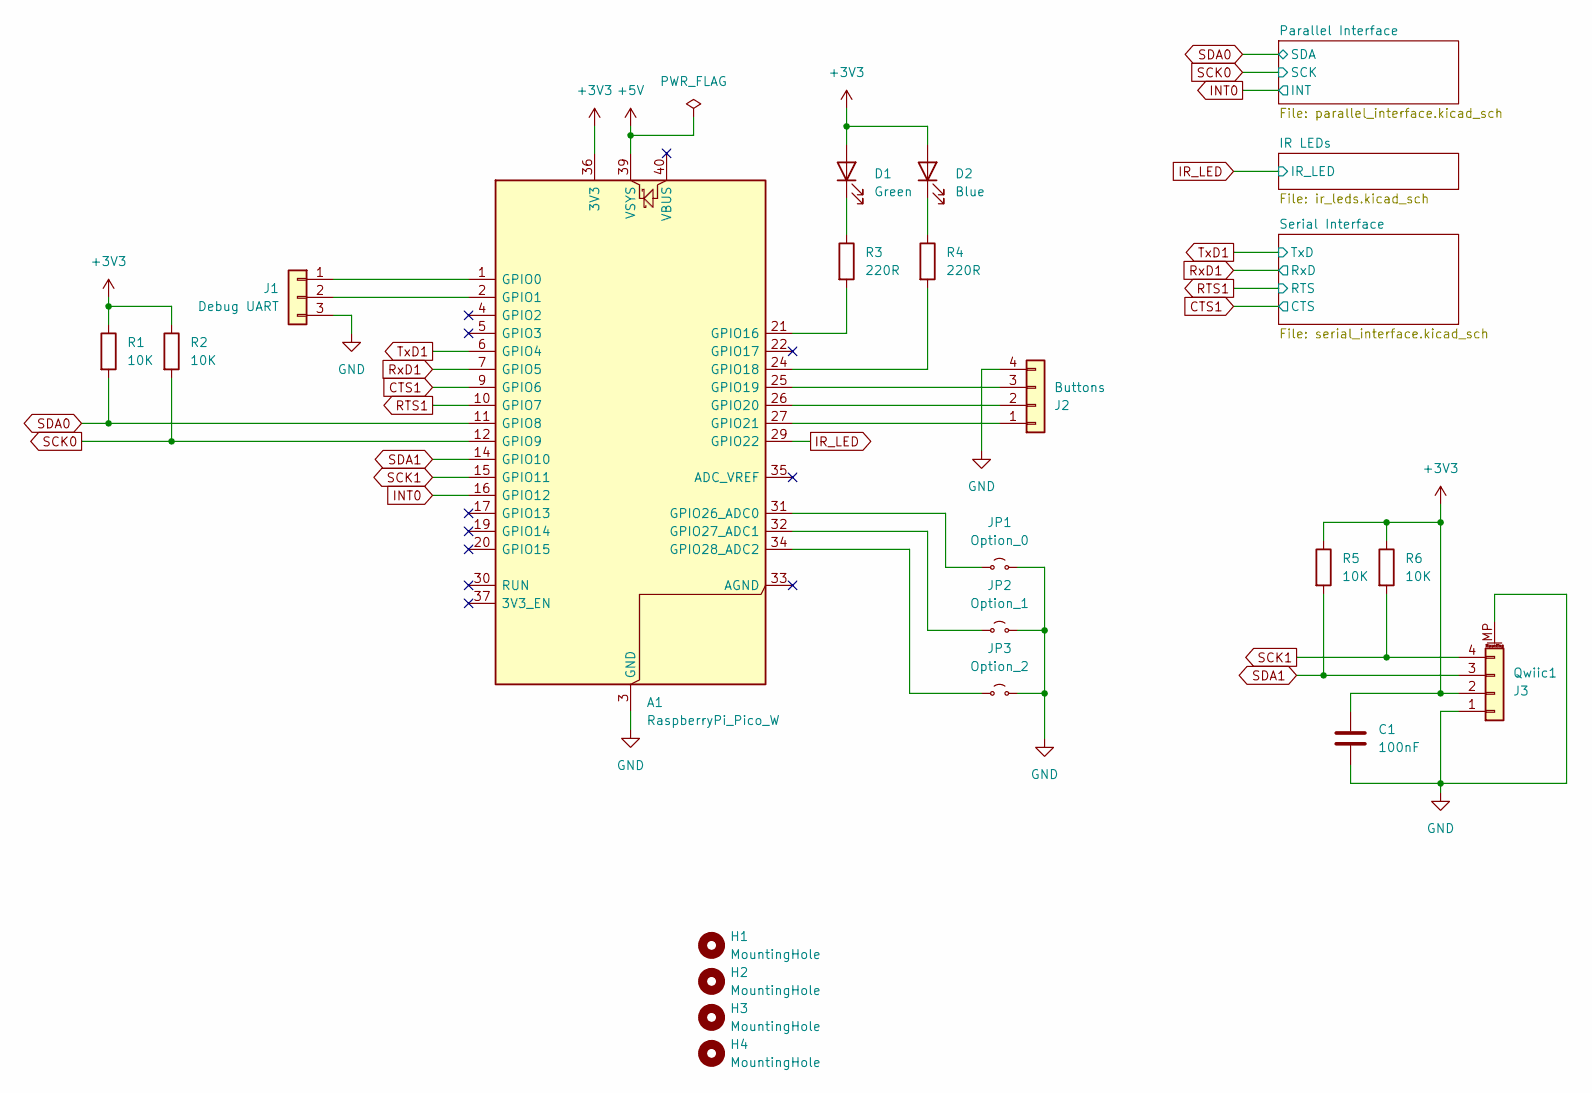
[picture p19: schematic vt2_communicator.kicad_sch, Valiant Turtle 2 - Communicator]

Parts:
A1: RaspberryPi_Pico_W; RaspberryPi_Pico_Common
C1: 100nF; C_0805_2012Metric_Pad1.18x1.45mm_HandSolder
D1: Green; LED_D5.0mm_Horizontal_O1.27mm_Z3.0mm_Clear
D2: Blue; LED_D5.0mm_Horizontal_O1.27mm_Z3.0mm_Clear
H1, H2, H3, H4: MountingHole; MountingHole_3.2mm_M3
J1: Debug UART; PinHeader_1x03_P2.54mm_Vertical
J2: Buttons; JST_XH_B4B-XH-A_1x04_P2.50mm_Vertical
J3: Qwiic1; JST_SH_BM04B-SRSS-TB_1x04-1MP_P1.00mm_Vertical
JP1: Option_0; PinHeader_1x02_P2.54mm_Vertical
JP2: Option_1; PinHeader_1x02_P2.54mm_Vertical
JP3: Option_2; PinHeader_1x02_P2.54mm_Vertical
R1, R2, R5, R6: 10K; R_0805_2012Metric_Pad1.20x1.40mm_HandSolder
R3, R4: 220R; R_0805_2012Metric_Pad1.20x1.40mm_HandSolder

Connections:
+3V3: A1.36 (3V3), C1.2, D1.2 (A), D2.2 (A), J3.2, R1.1, R2.1, R5.1, R6.1; also elsewhere on the board
+5V: A1.39 (VSYS); also elsewhere on the board
CTS1: A1.9 (GPIO6); also elsewhere on the board
GND: A1.3 (GND), A1.8 (GND), A1.13 (GND), A1.18 (GND), A1.23 (GND), A1.28 (GND), A1.38 (GND), C1.1, J1.3, J2.4, J3.1, J3.MP (MountPin), JP1.2 (B), JP2.2 (B), JP3.2 (B); also elsewhere on the board
INT0: A1.16 (GPIO12); also elsewhere on the board
IR_LED: A1.29 (GPIO22); also elsewhere on the board
unnamed: A1.1 (GPIO0), J1.1
unnamed: A1.2 (GPIO1), J1.2
unnamed: A1.21 (GPIO16), R3.2
unnamed: A1.24 (GPIO18), R4.2
unnamed: A1.25 (GPIO19), J2.3
unnamed: A1.26 (GPIO20), J2.2
unnamed: A1.27 (GPIO21), J2.1
unnamed: A1.31 (GPIO26_ADC0), JP1.1 (A)
unnamed: A1.32 (GPIO27_ADC1), JP2.1 (A)
unnamed: A1.34 (GPIO28_ADC2), JP3.1 (A)
unnamed: D1.1 (K), R3.1
unnamed: D2.1 (K), R4.1
RTS1: A1.10 (GPIO7); also elsewhere on the board
RxD1: A1.7 (GPIO5); also elsewhere on the board
SCK0: A1.12 (GPIO9), R2.2; also elsewhere on the board
SCK1: A1.15 (GPIO11), J3.4, R6.2
SDA0: A1.11 (GPIO8), R1.2; also elsewhere on the board
SDA1: A1.14 (GPIO10), J3.3, R5.2
TxD1: A1.6 (GPIO4); also elsewhere on the board

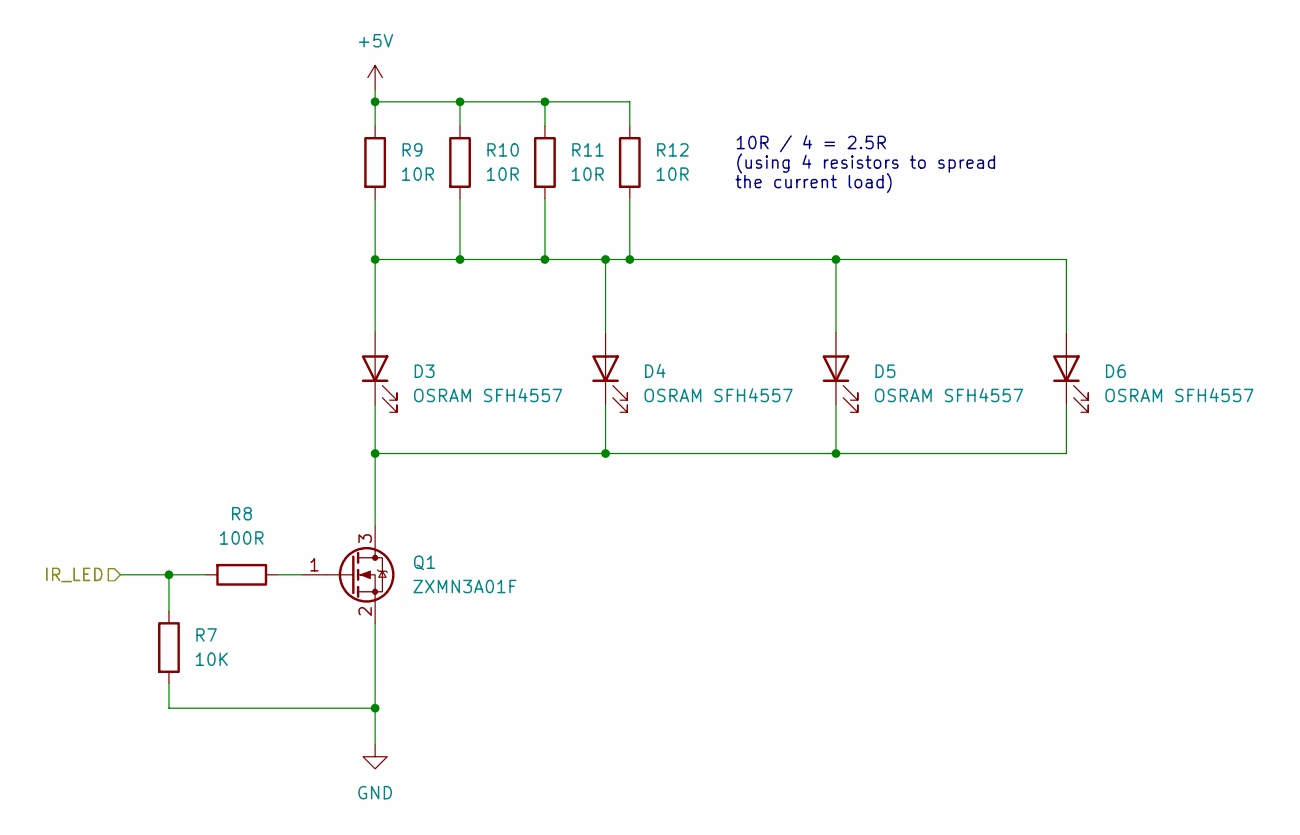
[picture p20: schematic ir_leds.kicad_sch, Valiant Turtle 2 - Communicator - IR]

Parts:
D3, D4, D5, D6: OSRAM SFH4557; LED_D5.0mm_Horizontal_O1.27mm_Z3.0mm_IRBlack
Q1: ZXMN3A01F; SOT-23
R7: 10K; R_0805_2012Metric_Pad1.20x1.40mm_HandSolder
R8: 100R; R_0805_2012Metric_Pad1.20x1.40mm_HandSolder
R9, R10, R11, R12: 10R; R_0805_2012Metric_Pad1.20x1.40mm_HandSolder

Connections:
+5V: R9.1, R10.1, R11.1, R12.1; also elsewhere on the board
GND: Q1.2 (S), R7.2; also elsewhere on the board
IR_LED: R7.1, R8.2; also elsewhere on the board
unnamed: D3.2 (A), D4.2 (A), D5.2 (A), D6.2 (A), R9.2, R10.2, R11.2, R12.2
unnamed: D3.1 (K), D4.1 (K), D5.1 (K), D6.1 (K), Q1.3 (D)
unnamed: Q1.1 (G), R8.1

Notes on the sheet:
10R / 4 = 2.5R (using 4 resistors to spread the current load)

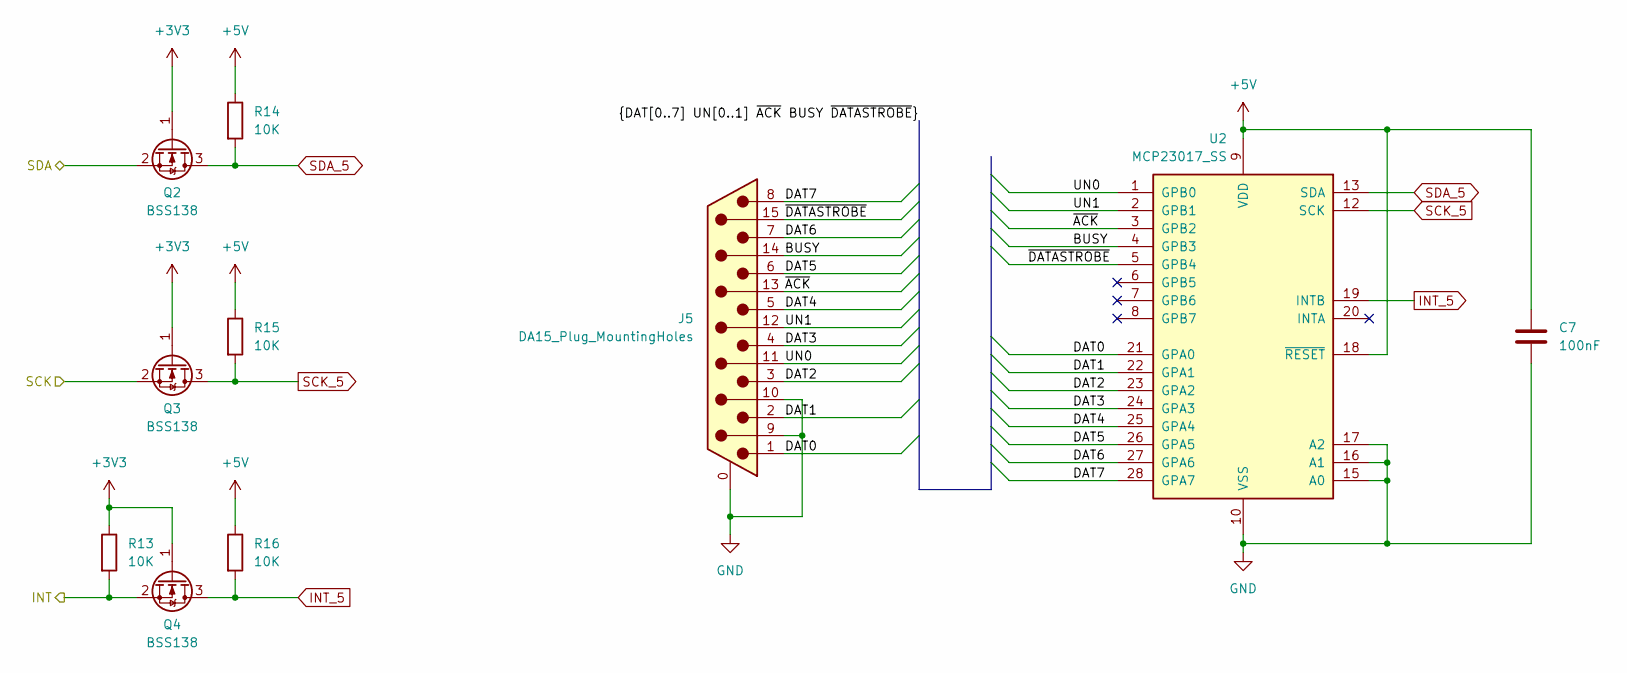
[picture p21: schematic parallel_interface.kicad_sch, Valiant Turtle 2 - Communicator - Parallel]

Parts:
C7: 100nF; C_0805_2012Metric_Pad1.18x1.45mm_HandSolder
J5: DA15_Plug_MountingHoles; DSUB-15_Male_Horizontal_P2.77x2.84mm_EdgePinOffset9.90mm_Ho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
Q2, Q3, Q4: BSS138; SOT-23
R13, R14, R15, R16: 10K; R_0805_2012Metric_Pad1.20x1.40mm_HandSolder
U2: MCP23017_SS; SSOP-28_5.3x10.2mm_P0.65mm

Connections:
+3V3: Q2.1 (G), Q3.1 (G), Q4.1 (G), R13.1; also elsewhere on the board
+5V: C7.1, R14.1, R15.1, R16.1, U2.9 (VDD), U2.18 (~RESET); also elsewhere on the board
/Parallel Interface/BUSY: J5.14, U2.4 (GPB3)
/Parallel Interface/DAT0: J5.1, U2.21 (GPA0)
/Parallel Interface/DAT1: J5.2, U2.22 (GPA1)
/Parallel Interface/DAT2: J5.3, U2.23 (GPA2)
/Parallel Interface/DAT3: J5.4, U2.24 (GPA3)
/Parallel Interface/DAT4: J5.5, U2.25 (GPA4)
/Parallel Interface/DAT5: J5.6, U2.26 (GPA5)
/Parallel Interface/DAT6: J5.7, U2.27 (GPA6)
/Parallel Interface/DAT7: J5.8, U2.28 (GPA7)
/Parallel Interface/UN0: J5.11 (P111), U2.1 (GPB0)
/Parallel Interface/UN1: J5.12, U2.2 (GPB1)
/Parallel Interface/~ACK: J5.13, U2.3 (GPB2)
/Parallel Interface/~DATASTROBE: J5.15, U2.5 (GPB4)
GND: C7.2, J5.0 (PAD), J5.9, J5.10, U2.10 (VSS), U2.15 (A0), U2.16 (A1), U2.17 (A2); also elsewhere on the board
INT0: Q4.2 (S), R13.2; also elsewhere on the board
INT_5: Q4.3 (D), R16.2, U2.19 (INTB)
SCK0: Q3.2 (S); also elsewhere on the board
SCK_5: Q3.3 (D), R15.2, U2.12 (SCK)
SDA0: Q2.2 (S); also elsewhere on the board
SDA_5: Q2.3 (D), R14.2, U2.13 (SDA)

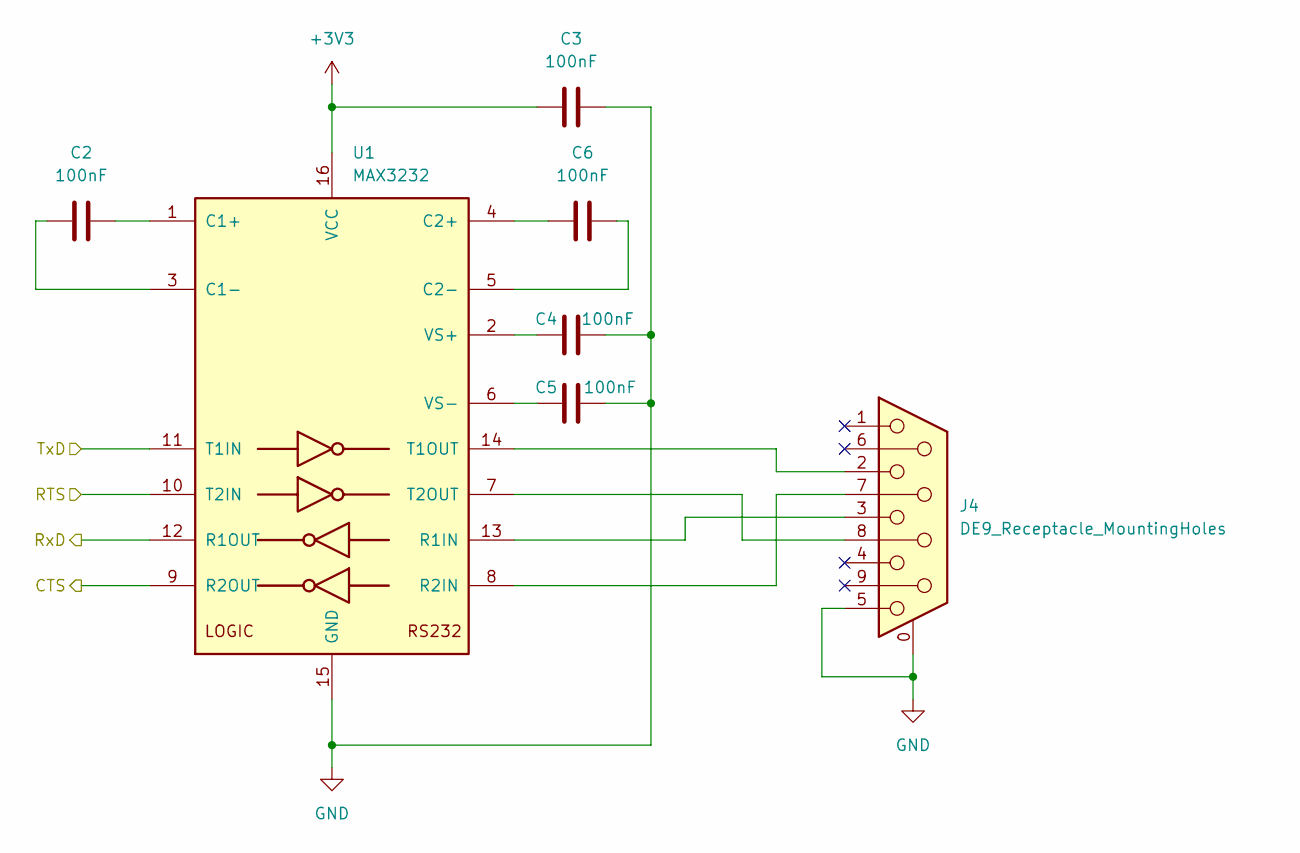
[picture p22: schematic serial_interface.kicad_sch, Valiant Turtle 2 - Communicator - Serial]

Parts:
C2, C3, C4, C5, C6: 100nF; C_0805_2012Metric_Pad1.18x1.45mm_HandSolder
J4: DE9_Receptacle_MountingHoles; DSUB-9_Female_Horizontal_P2.77x2.84mm_EdgePinOffset9.90mm_H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
U1: MAX3232; SOIC-16_3.9x9.9mm_P1.27mm

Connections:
+3V3: C3.1, U1.16 (VCC); also elsewhere on the board
CTS1: U1.9 (R2OUT); also elsewhere on the board
GND: C3.2, C4.2, C5.2, J4.0 (PAD), J4.5, U1.15 (GND); also elsewhere on the board
unnamed: C2.2, U1.1 (C1+)
unnamed: C2.1, U1.3 (C1-)
unnamed: C6.1, U1.4 (C2+)
unnamed: C6.2, U1.5 (C2-)
unnamed: J4.3, U1.13 (R1IN)
unnamed: J4.7, U1.8 (R2IN)
unnamed: J4.2, U1.14 (T1OUT)
unnamed: J4.8, U1.7 (T2OUT)
unnamed: C4.1, U1.2 (VS+)
unnamed: C5.1, U1.6 (VS-)
RTS1: U1.10 (T2IN); also elsewhere on the board
RxD1: U1.12 (R1OUT); also elsewhere on the board
TxD1: U1.11 (T1IN); also elsewhere on the board

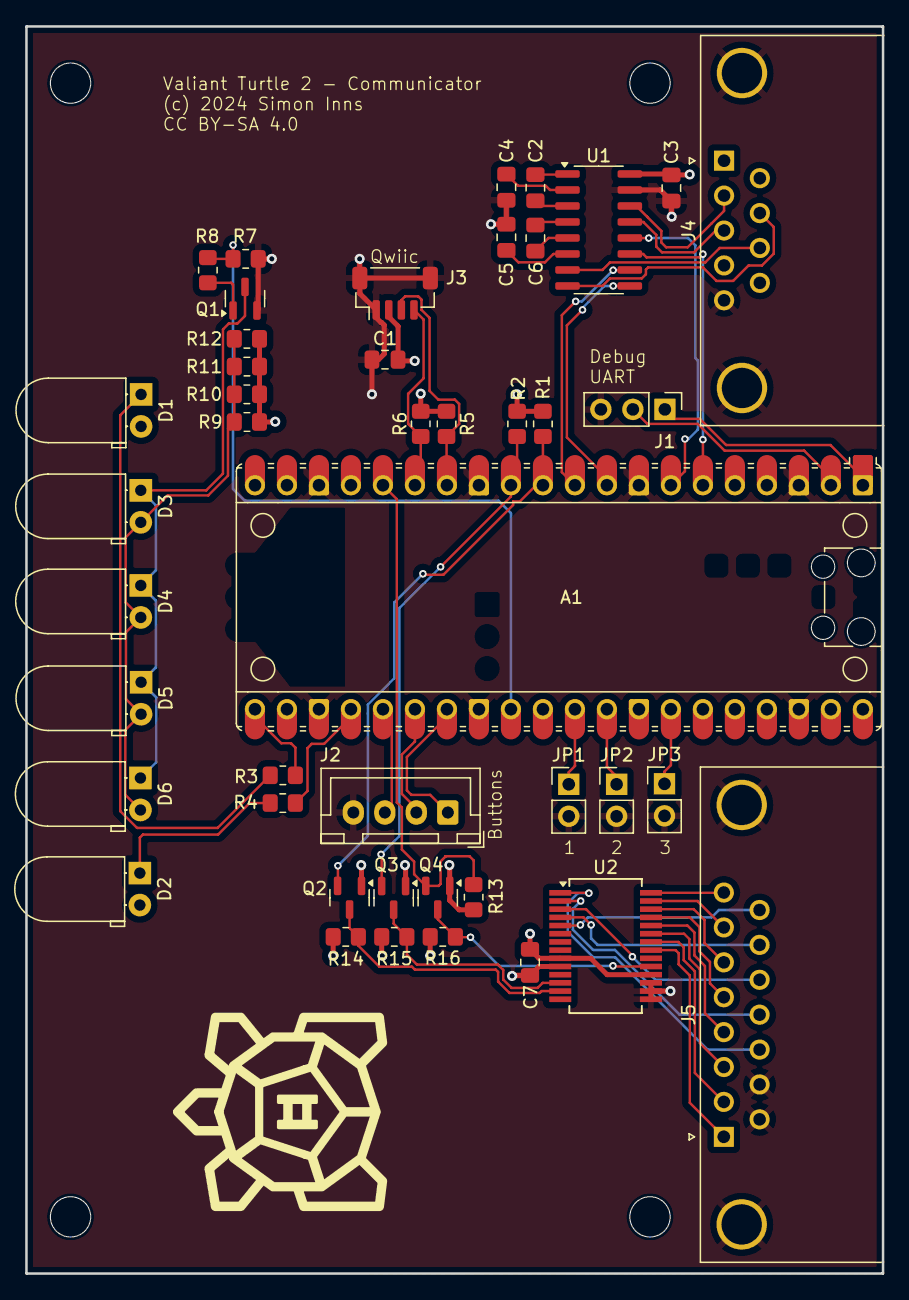
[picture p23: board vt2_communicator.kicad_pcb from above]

Board: 4 copper layers, 68.0 x 99.0 mm, 48 parts (0 on the bottom side), 54 nets.

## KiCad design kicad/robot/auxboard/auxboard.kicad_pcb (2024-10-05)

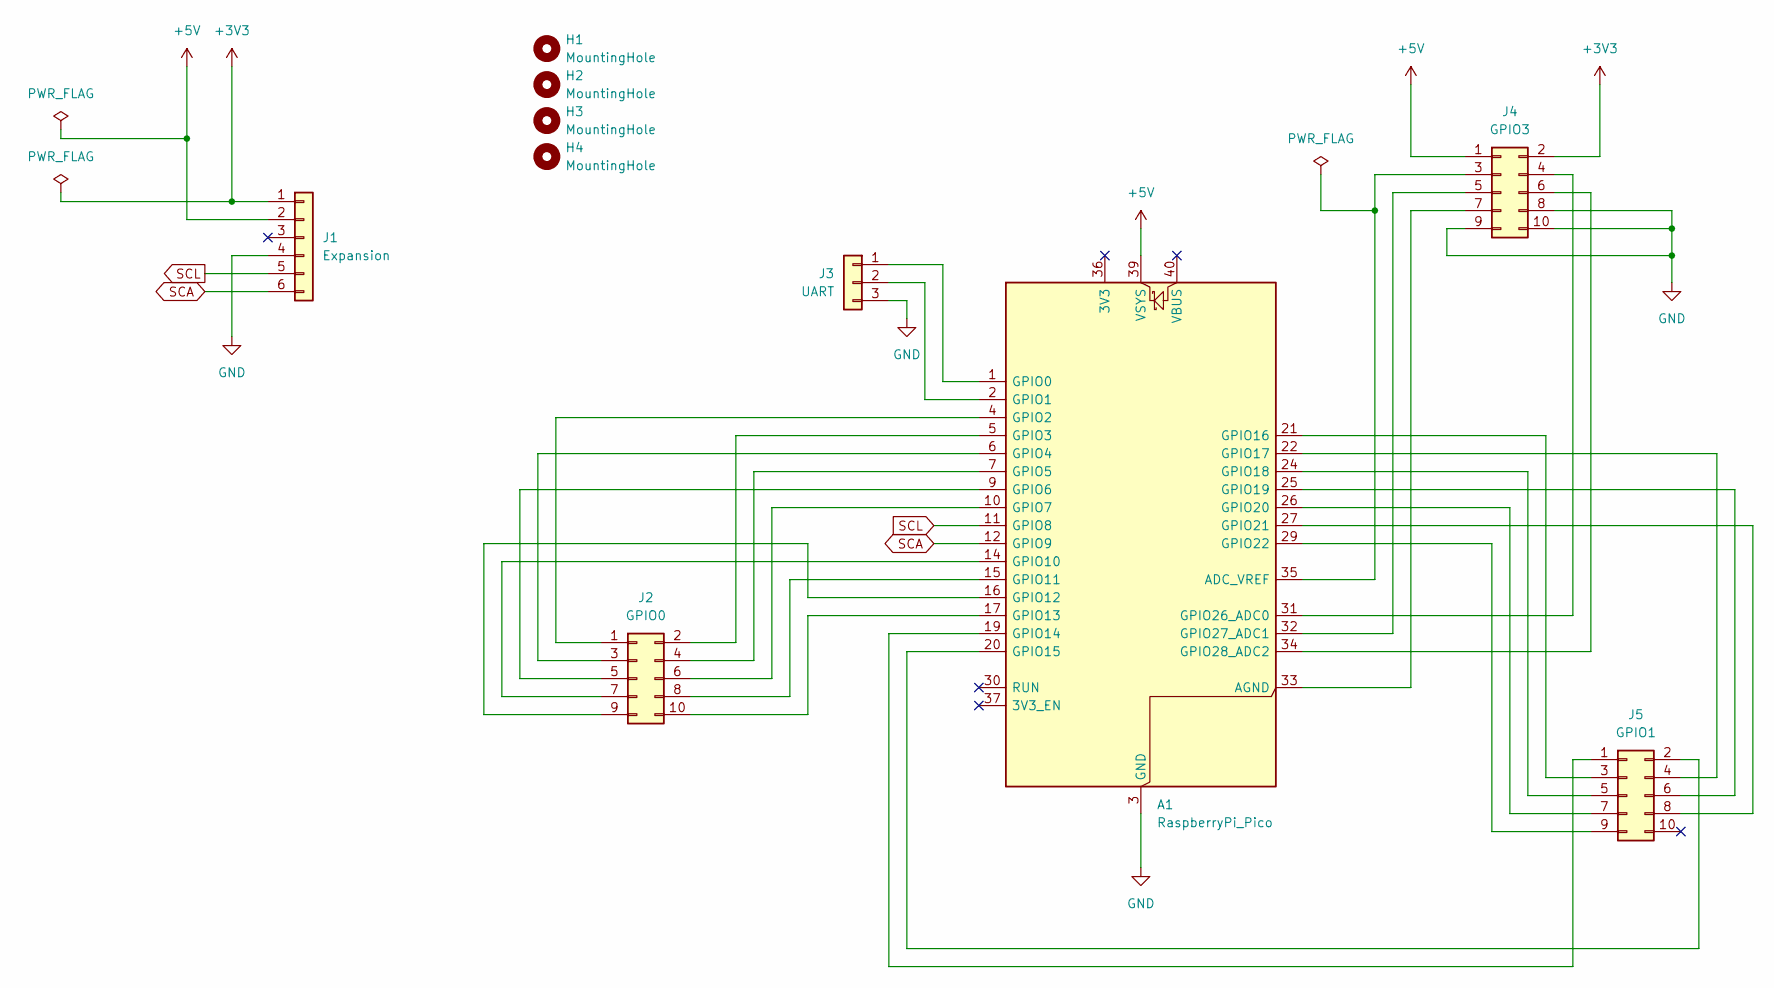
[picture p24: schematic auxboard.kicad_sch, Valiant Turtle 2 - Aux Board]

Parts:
A1: RaspberryPi_Pico; RaspberryPi_Pico_Common
H1, H2, H3, H4: MountingHole; MountingHole_3.2mm_M3
J1: Expansion; JST_XH_B6B-XH-A_1x06_P2.50mm_Vertical
J2: GPIO0; IDC-Header_2x05_P2.54mm_Vertical
J3: UART; PinHeader_1x03_P2.54mm_Vertical
J4: GPIO3; IDC-Header_2x05_P2.54mm_Vertical
J5: GPIO1; IDC-Header_2x05_P2.54mm_Vertical

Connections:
+3V3: J1.1, J4.2
+5V: A1.39 (VSYS), J1.2, J4.1
GND: A1.3 (GND), A1.8 (GND), A1.13 (GND), A1.18 (GND), A1.23 (GND), A1.28 (GND), A1.38 (GND), J1.4, J3.3, J4.8, J4.9, J4.10
unnamed: A1.35 (ADC_VREF), J4.3
unnamed: A1.33 (AGND), J4.7
unnamed: A1.1 (GPIO0), J3.1
unnamed: A1.2 (GPIO1), J3.2
unnamed: A1.4 (GPIO2), J2.1
unnamed: A1.5 (GPIO3), J2.2
unnamed: A1.6 (GPIO4), J2.3
unnamed: A1.7 (GPIO5), J2.4
unnamed: A1.9 (GPIO6), J2.5
unnamed: A1.10 (GPIO7), J2.6
unnamed: A1.14 (GPIO10), J2.7
unnamed: A1.15 (GPIO11), J2.8
unnamed: A1.16 (GPIO12), J2.9
unnamed: A1.17 (GPIO13), J2.10
unnamed: A1.19 (GPIO14), J5.1
unnamed: A1.20 (GPIO15), J5.2
unnamed: A1.21 (GPIO16), J5.3
unnamed: A1.22 (GPIO17), J5.4
unnamed: A1.24 (GPIO18), J5.5
unnamed: A1.25 (GPIO19), J5.6
unnamed: A1.26 (GPIO20), J5.7
unnamed: A1.27 (GPIO21), J5.8
unnamed: A1.29 (GPIO22), J5.9
unnamed: A1.31 (GPIO26_ADC0), J4.4
unnamed: A1.32 (GPIO27_ADC1), J4.5
unnamed: A1.34 (GPIO28_ADC2), J4.6
SCA: A1.12 (GPIO9), J1.6
SCL: A1.11 (GPIO8), J1.5

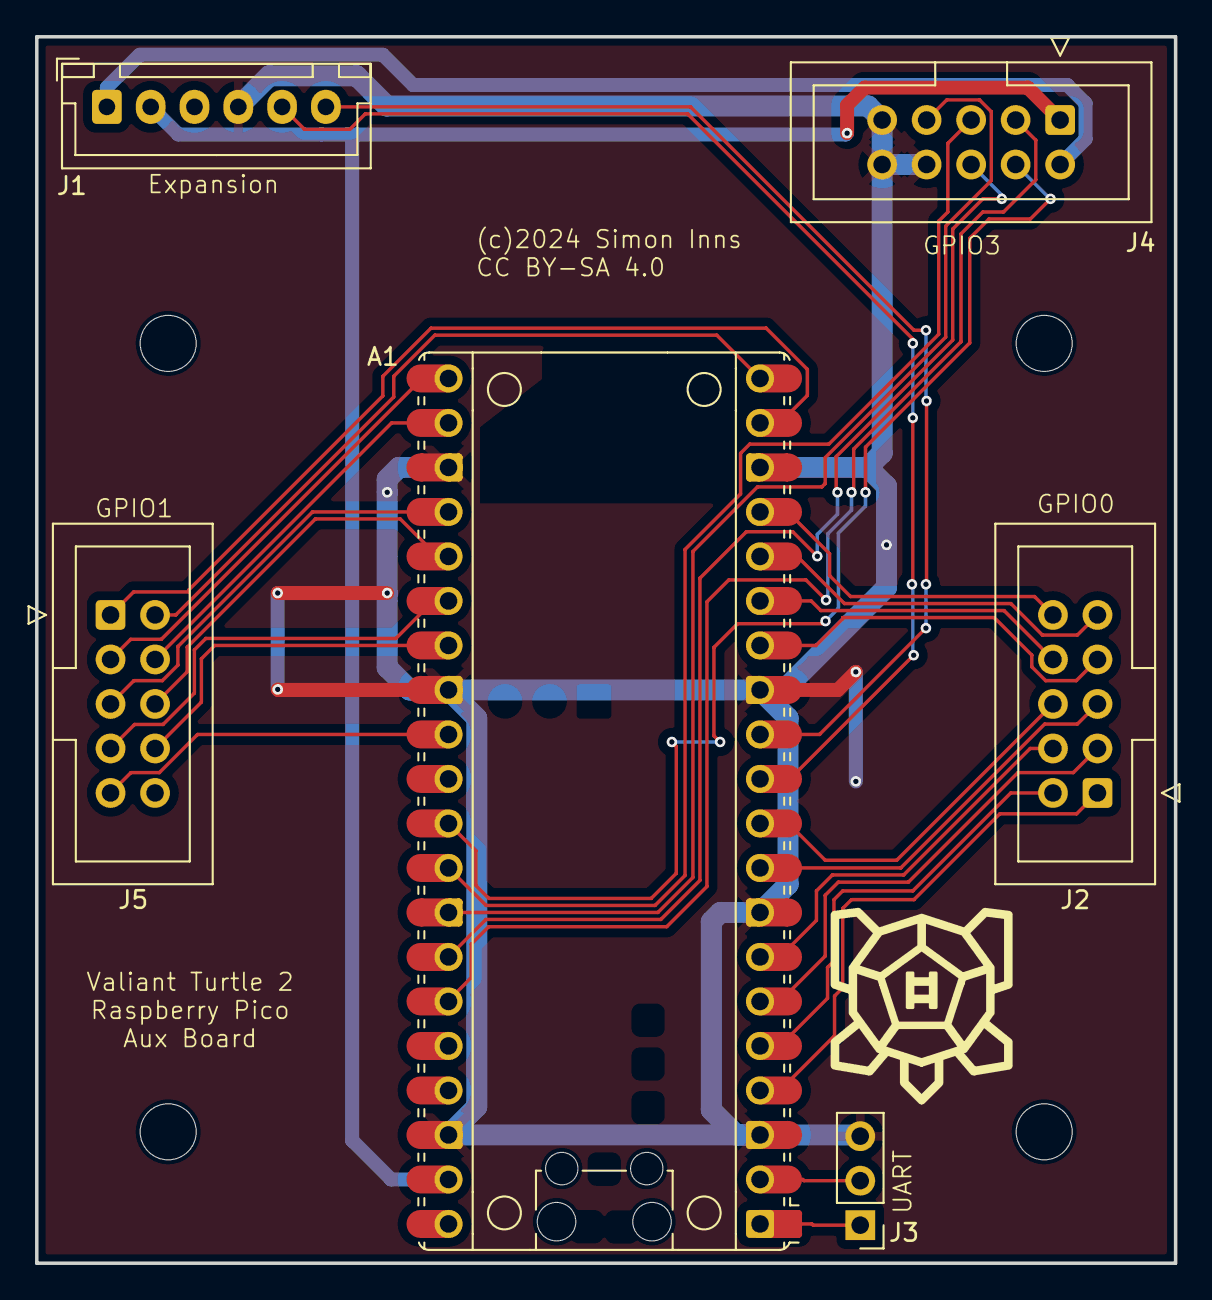
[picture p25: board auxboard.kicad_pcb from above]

Board: 2 copper layers, 65.0 x 70.0 mm, 10 parts (0 on the bottom side), 31 nets.

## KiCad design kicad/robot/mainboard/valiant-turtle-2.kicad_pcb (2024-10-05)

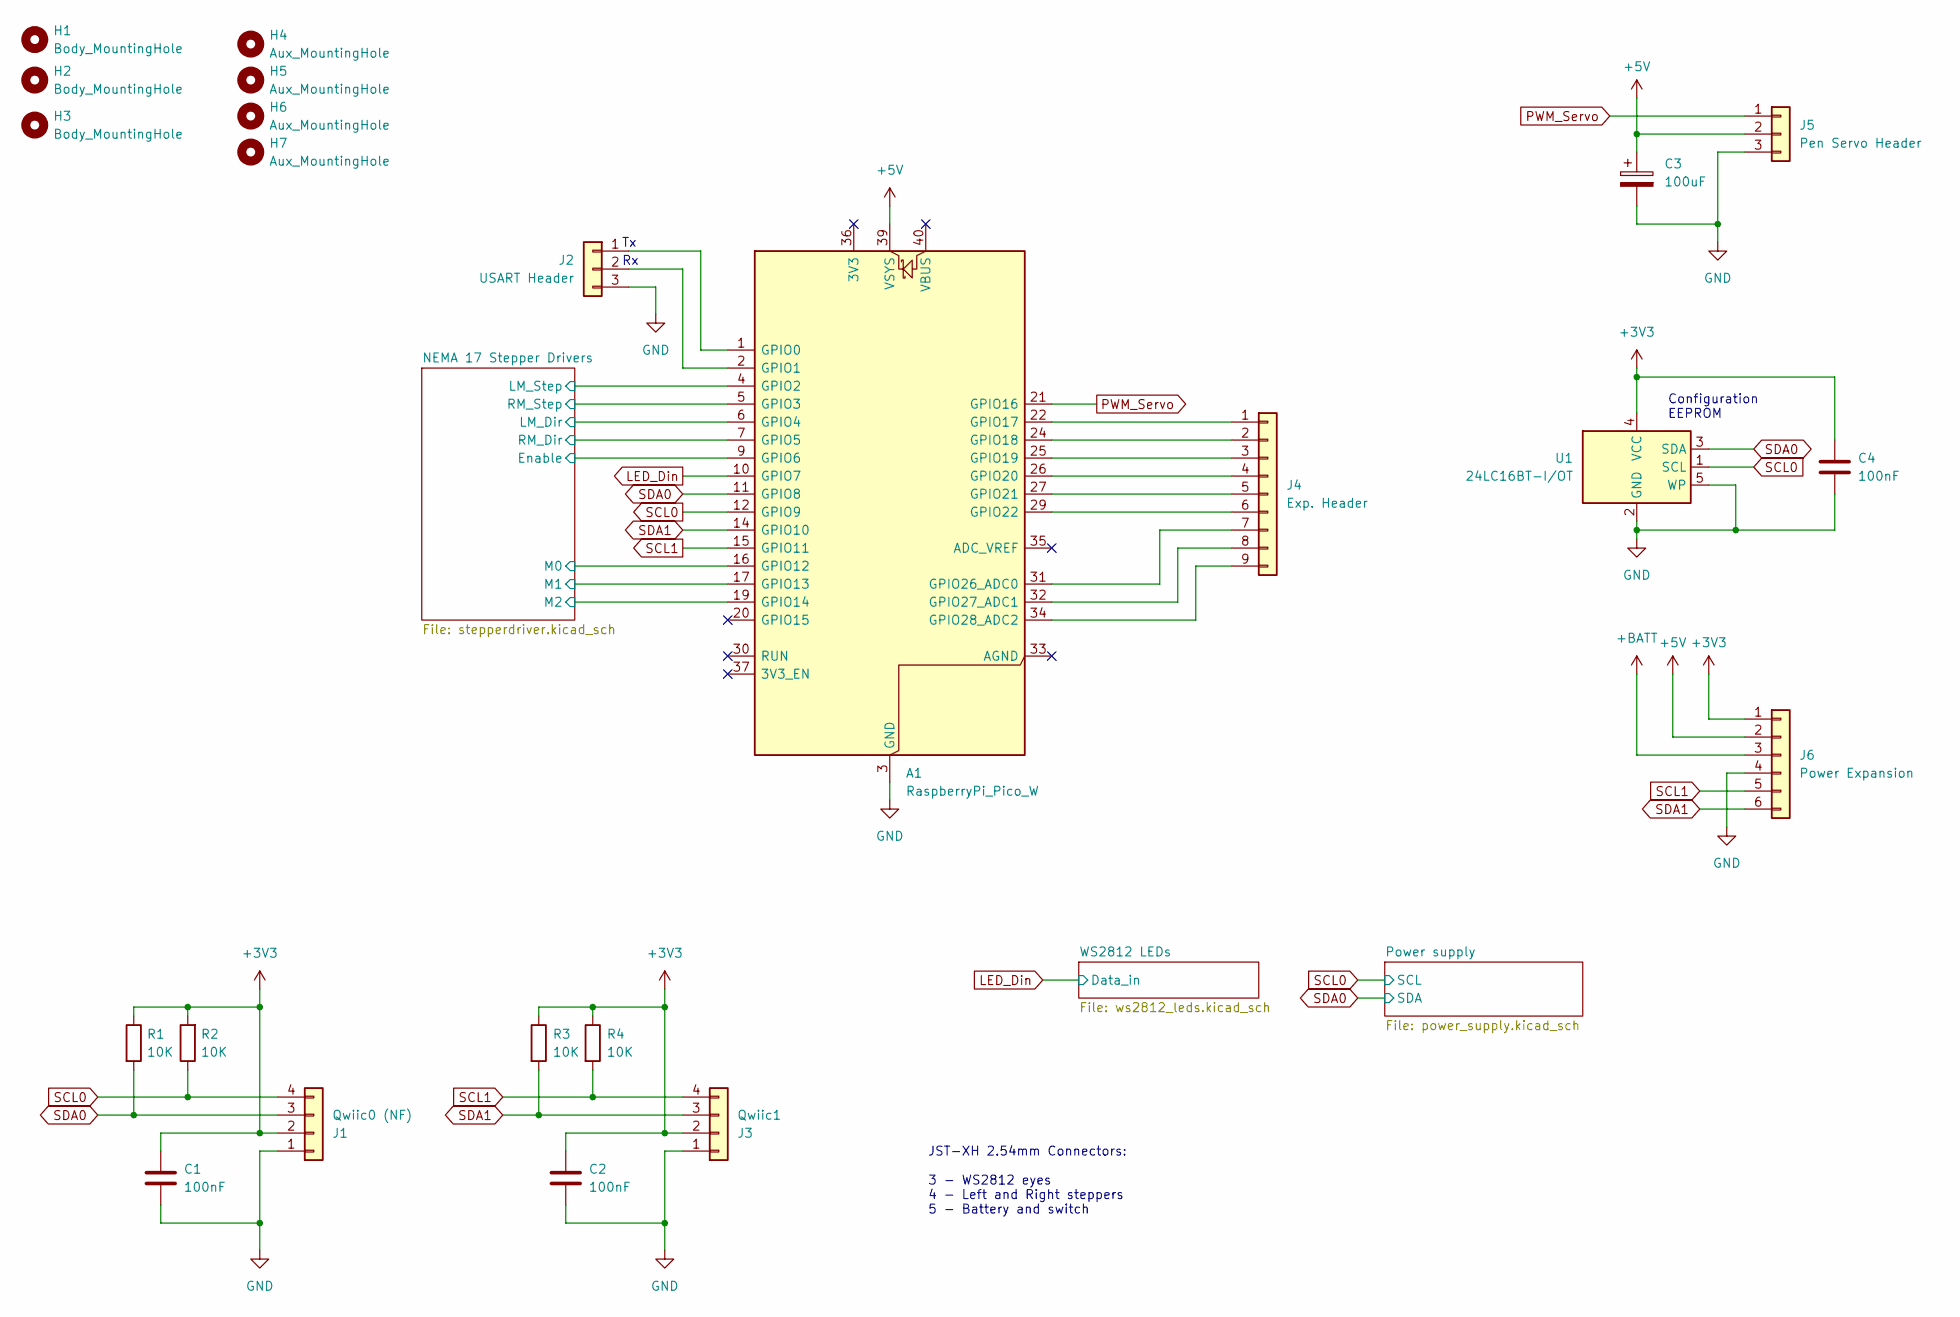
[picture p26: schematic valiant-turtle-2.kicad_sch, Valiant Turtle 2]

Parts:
A1: RaspberryPi_Pico_W; RaspberryPi_Pico_Common
C1, C2, C4: 100nF; C_0805_2012Metric_Pad1.18x1.45mm_HandSolder
C3: 100uF; CP_Elec_8x6.2
H1, H2, H3: Body_MountingHole; MountingHole_3.2mm_M3
H4, H5, H6, H7: Aux_MountingHole; MountingHole_3.2mm_M3
J1: Qwiic0 (NF); JST_SH_SM04B-SRSS-TB_1x04-1MP_P1.00mm_Horizontal
J2: USART Header; PinHeader_1x03_P2.54mm_Vertical
J3: Qwiic1; JST_SH_SM04B-SRSS-TB_1x04-1MP_P1.00mm_Horizontal
J4: Exp. Header; PinHeader_1x09_P2.54mm_Vertical
J5: Pen Servo Header; PinHeader_1x03_P2.54mm_Vertical
J6: Power Expansion; JST_XH_B6B-XH-A_1x06_P2.50mm_Vertical
R1, R2, R3, R4: 10K; R_0805_2012Metric_Pad1.20x1.40mm_HandSolder
U1: 24LC16BT-I/OT; SOT-23-5

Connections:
+3V3: C1.1, C2.1, C4.1, J1.2, J3.2, J6.1, R1.1, R2.2, R3.1, R4.1, U1.4 (VCC); also elsewhere on the board
+5V: A1.39 (VSYS), C3.1, J5.2, J6.2; also elsewhere on the board
+BATT: J6.3; also elsewhere on the board
/NEMA 17 Stepper Drivers/Enable: A1.9 (GPIO6); also elsewhere on the board
/NEMA 17 Stepper Drivers/LM_Dir: A1.6 (GPIO4); also elsewhere on the board
/NEMA 17 Stepper Drivers/LM_Step: A1.4 (GPIO2); also elsewhere on the board
/NEMA 17 Stepper Drivers/M0: A1.16 (GPIO12); also elsewhere on the board
/NEMA 17 Stepper Drivers/M1: A1.17 (GPIO13); also elsewhere on the board
/NEMA 17 Stepper Drivers/M2: A1.19 (GPIO14); also elsewhere on the board
/NEMA 17 Stepper Drivers/RM_Dir: A1.7 (GPIO5); also elsewhere on the board
/NEMA 17 Stepper Drivers/RM_Step: A1.5 (GPIO3); also elsewhere on the board
GND: A1.3 (GND), A1.8 (GND), A1.13 (GND), A1.18 (GND), A1.23 (GND), A1.28 (GND), A1.38 (GND), C1.2, C2.2, C3.2, C4.2, J1.1, J2.3, J3.1, J5.3, J6.4, U1.2 (GND), U1.5 (WP); also elsewhere on the board
LED_Din: A1.10 (GPIO7); also elsewhere on the board
unnamed: A1.1 (GPIO0), J2.1
unnamed: A1.2 (GPIO1), J2.2
unnamed: A1.22 (GPIO17), J4.1
unnamed: A1.24 (GPIO18), J4.2
unnamed: A1.25 (GPIO19), J4.3
unnamed: A1.26 (GPIO20), J4.4
unnamed: A1.27 (GPIO21), J4.5
unnamed: A1.29 (GPIO22), J4.6
unnamed: A1.31 (GPIO26_ADC0), J4.7
unnamed: A1.32 (GPIO27_ADC1), J4.8
unnamed: A1.34 (GPIO28_ADC2), J4.9
PWM_Servo: A1.21 (GPIO16), J5.1
SCL0: A1.12 (GPIO9), J1.4, R2.1, U1.1 (SCL); also elsewhere on the board
SCL1: A1.15 (GPIO11), J3.4, J6.5, R4.2
SDA0: A1.11 (GPIO8), J1.3, R1.2, U1.3 (SDA); also elsewhere on the board
SDA1: A1.14 (GPIO10), J3.3, J6.6, R3.2

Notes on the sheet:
JST-XH 2.54mm Connectors: 3 - WS2812 eyes 4 - Left and Right steppers 5 - Battery and switch
Configuration EEPROM

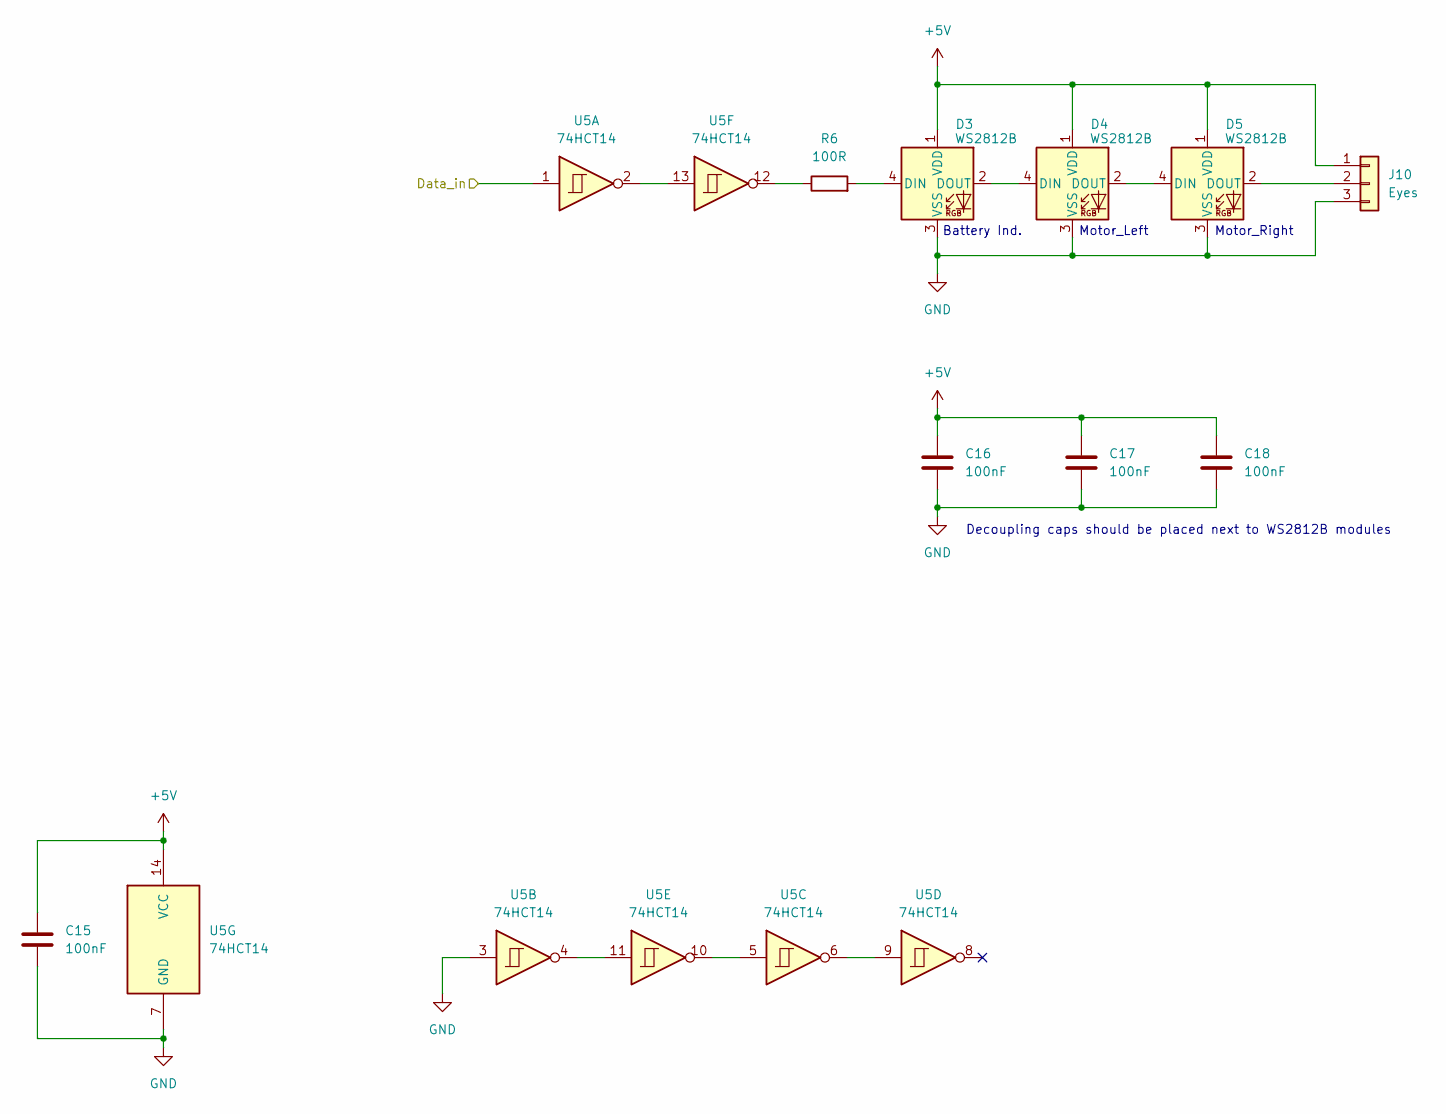
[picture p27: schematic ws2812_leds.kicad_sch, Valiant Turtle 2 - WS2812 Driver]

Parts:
C15, C16, C17, C18: 100nF; C_0805_2012Metric_Pad1.18x1.45mm_HandSolder
D3, D4, D5: WS2812B; LED_WS2812B_PLCC4_5.0x5.0mm_P3.2mm
J10: Eyes; JST_XH_B3B-XH-A_1x03_P2.50mm_Vertical
R6: 100R; R_0805_2012Metric_Pad1.20x1.40mm_HandSolder
U5: 74HCT14; SO-14_3.9x8.65mm_P1.27mm

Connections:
+5V: C15.1, C16.1, C17.1, C18.1, D3.1 (VDD), D4.1 (VDD), D5.1 (VDD), J10.1, U5.14 (VCC); also elsewhere on the board
GND: C15.2, C16.2, C17.2, C18.2, D3.3 (VSS), D4.3 (VSS), D5.3 (VSS), J10.3, U5.3, U5.7 (GND); also elsewhere on the board
LED_Din: U5.1; also elsewhere on the board
unnamed: D3.4 (DIN), R6.2
unnamed: D3.2 (DOUT), D4.4 (DIN)
unnamed: D4.2 (DOUT), D5.4 (DIN)
unnamed: D5.2 (DOUT), J10.2
unnamed: R6.1, U5.12
unnamed: U5.6, U5.9
unnamed: U5.5, U5.10
unnamed: U5.4, U5.11
unnamed: U5.2, U5.13

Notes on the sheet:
Motor_Right
Motor_Left
Battery Ind.
Decoupling caps should be placed next to WS2812B modules

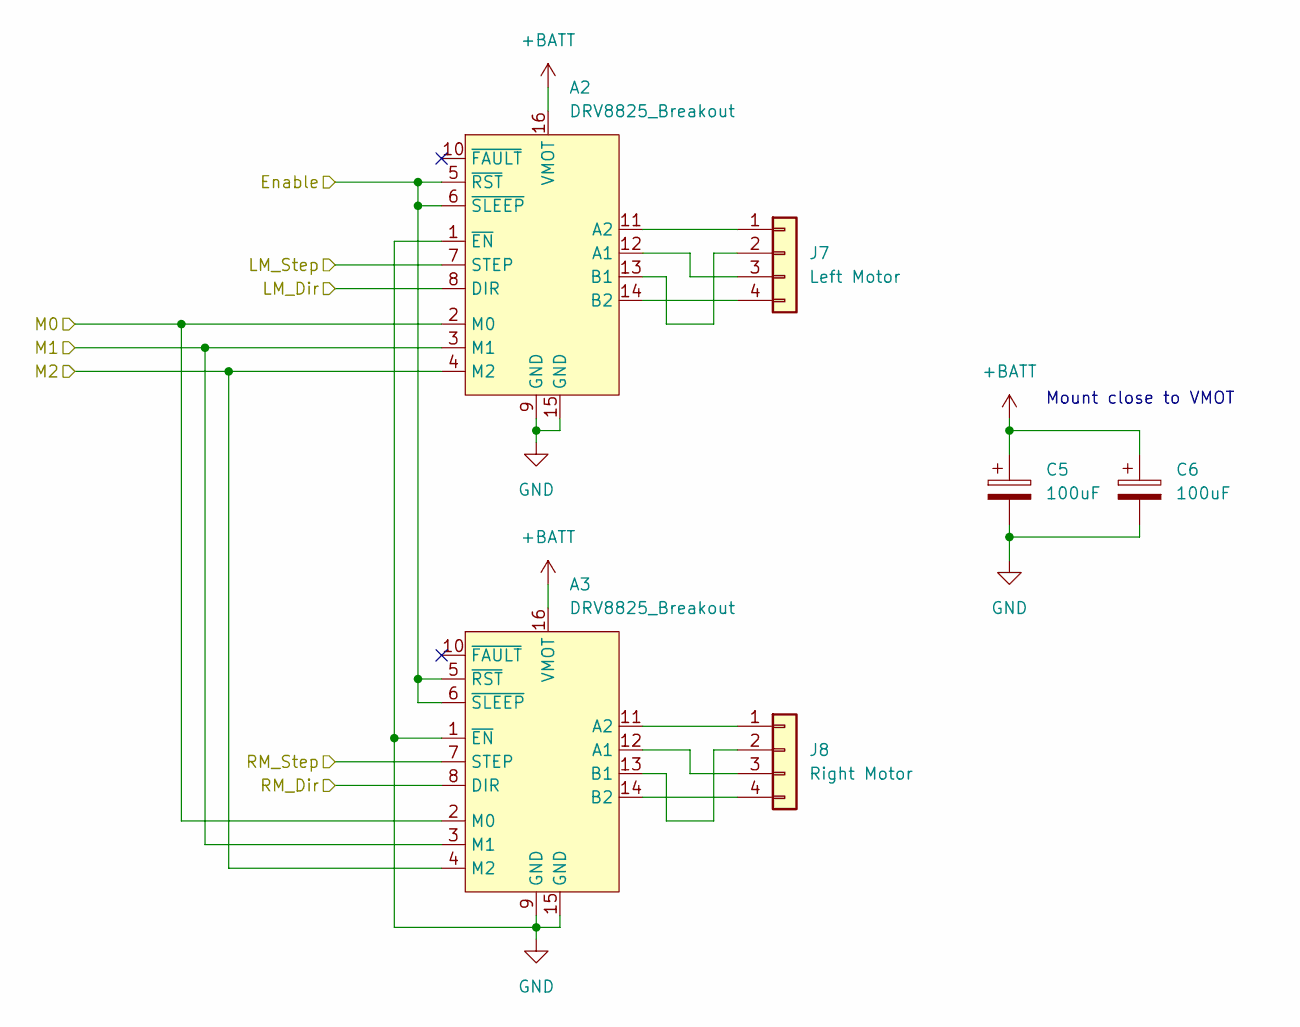
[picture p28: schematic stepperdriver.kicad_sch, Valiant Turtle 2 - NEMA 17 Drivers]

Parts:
A2, A3: DRV8825_Breakout; Pololu_Breakout-16_15.2x20.3mm
C5, C6: 100uF; CP_Elec_8x6.2
J7: Left Motor; JST_XH_B4B-XH-A_1x04_P2.50mm_Vertical
J8: Right Motor; JST_XH_B4B-XH-A_1x04_P2.50mm_Vertical

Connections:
+BATT: A2.16 (VMOT), A3.16 (VMOT), C5.1, C6.1; also elsewhere on the board
/NEMA 17 Stepper Drivers/Enable: A2.5 (~RST), A2.6 (~SLEEP), A3.5 (~RST), A3.6 (~SLEEP); also elsewhere on the board
/NEMA 17 Stepper Drivers/LM_Dir: A2.8 (DIR); also elsewhere on the board
/NEMA 17 Stepper Drivers/LM_Step: A2.7 (STEP); also elsewhere on the board
/NEMA 17 Stepper Drivers/M0: A2.2 (M0), A3.2 (M0); also elsewhere on the board
/NEMA 17 Stepper Drivers/M1: A2.3 (M1), A3.3 (M1); also elsewhere on the board
/NEMA 17 Stepper Drivers/M2: A2.4 (M2), A3.4 (M2); also elsewhere on the board
/NEMA 17 Stepper Drivers/RM_Dir: A3.8 (DIR); also elsewhere on the board
/NEMA 17 Stepper Drivers/RM_Step: A3.7 (STEP); also elsewhere on the board
GND: A2.1 (~EN), A2.9 (GND), A2.15 (GND), A3.1 (~EN), A3.9 (GND), A3.15 (GND), C5.2, C6.2; also elsewhere on the board
unnamed: A2.12 (A1), J7.3
unnamed: A2.11 (A2), J7.1
unnamed: A2.13 (B1), J7.2
unnamed: A2.14 (B2), J7.4
unnamed: A3.12 (A1), J8.3
unnamed: A3.11 (A2), J8.1
unnamed: A3.13 (B1), J8.2
unnamed: A3.14 (B2), J8.4

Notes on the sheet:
Mount close to VMOT

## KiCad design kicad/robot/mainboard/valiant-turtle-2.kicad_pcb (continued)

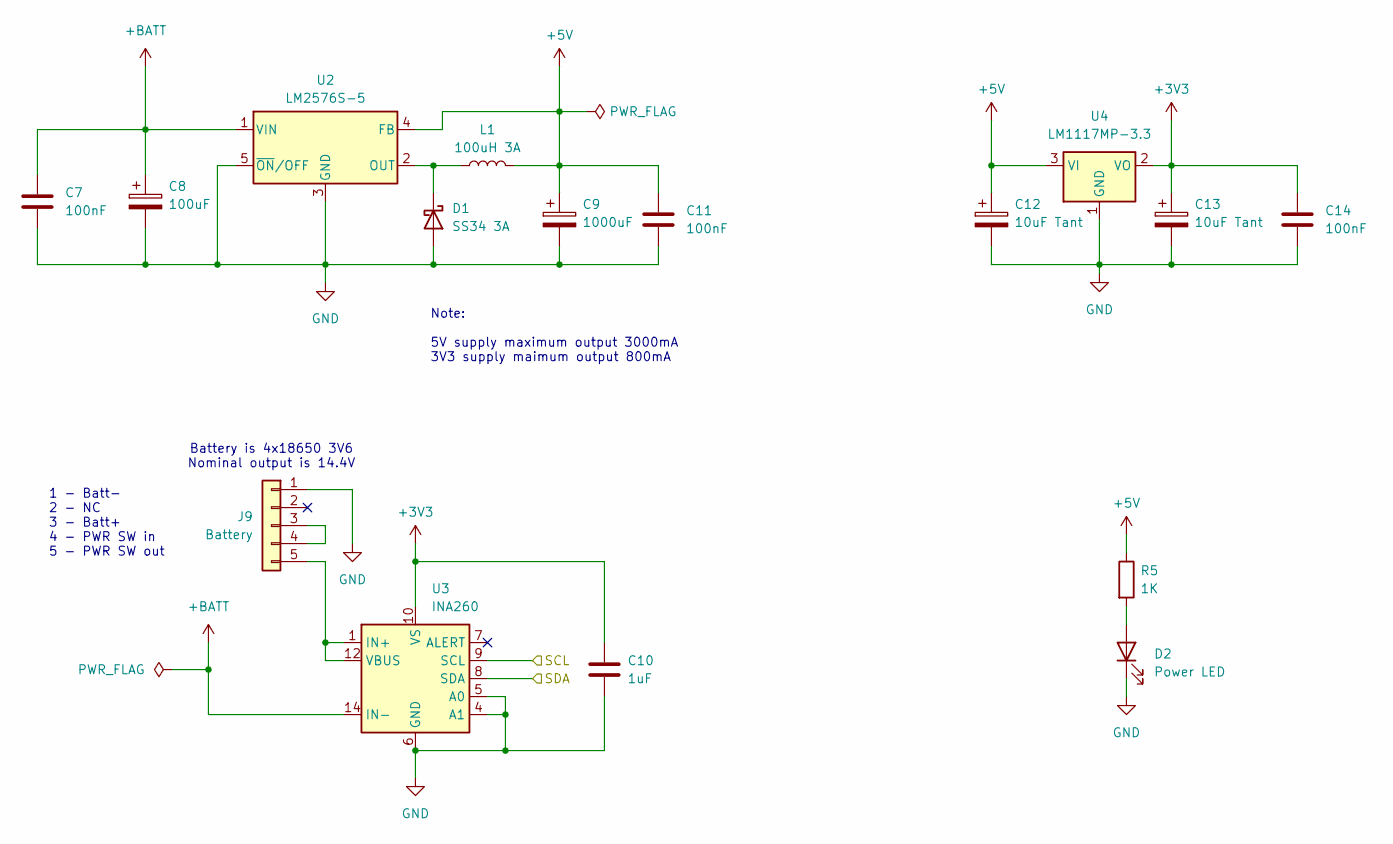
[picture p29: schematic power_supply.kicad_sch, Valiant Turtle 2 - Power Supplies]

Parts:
C7, C11, C14: 100nF; C_0805_2012Metric_Pad1.18x1.45mm_HandSolder
C8: 100uF; CP_Elec_8x6.2
C9: 1000uF; CP_Elec_10x10.5
C10: 1uF; C_0805_2012Metric_Pad1.18x1.45mm_HandSolder
C12, C13: 10uF Tant; CP_EIA-3528-21_Kemet-B_Pad1.50x2.35mm_HandSolder
D1: SS34 3A; D_SMC_Handsoldering
D2: Power LED; LED_0805_2012Metric_Pad1.15x1.40mm_HandSolder
J9: Battery; JST_XH_B5B-XH-A_1x05_P2.50mm_Vertical
L1: 100uH 3A; Inductor_SDR1307
R5: 1K; R_0805_2012Metric_Pad1.20x1.40mm_HandSolder
U2: LM2576S-5; TO-263-5_TabPin3
U3: INA260; TSSOP-16_4.4x5mm_P0.65mm
U4: LM1117MP-3.3; SOT-223-3_TabPin2

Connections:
+3V3: C10.1, C13.1, C14.1, U3.10 (VS), U4.2 (VO); also elsewhere on the board
+5V: C9.1, C11.1, C12.1, L1.2, R5.1, U2.4 (FB), U4.3 (VI); also elsewhere on the board
+BATT: C7.1, C8.1, U2.1 (VIN), U3.14 (IN-), U3.15 (IN-), U3.16 (IN-); also elsewhere on the board
GND: C7.2, C8.2, C9.2, C10.2, C11.2, C12.2, C13.2, C14.2, D1.2 (A), D2.1 (K), J9.1, U2.3 (GND), U2.5 (~ON/OFF), U3.4 (A1), U3.5 (A0), U3.6 (GND), U3.11 (GND), U4.1 (GND); also elsewhere on the board
unnamed: D1.1 (K), L1.1, U2.2 (OUT)
unnamed: D2.2 (A), R5.2
unnamed: J9.3, J9.4
unnamed: J9.5, U3.1 (IN+), U3.2 (IN+), U3.3 (IN+), U3.12 (VBUS)
SCL0: U3.9 (SCL); also elsewhere on the board
SDA0: U3.8 (SDA); also elsewhere on the board

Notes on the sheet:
Battery is 4x18650 3V6 Nominal output is 14.4V
1 - Batt- 2 - NC 3 - Batt+ 4 - PWR SW in 5 - PWR SW out
Note: 5V supply maximum output 3000mA 3V3 supply maimum output 800mA

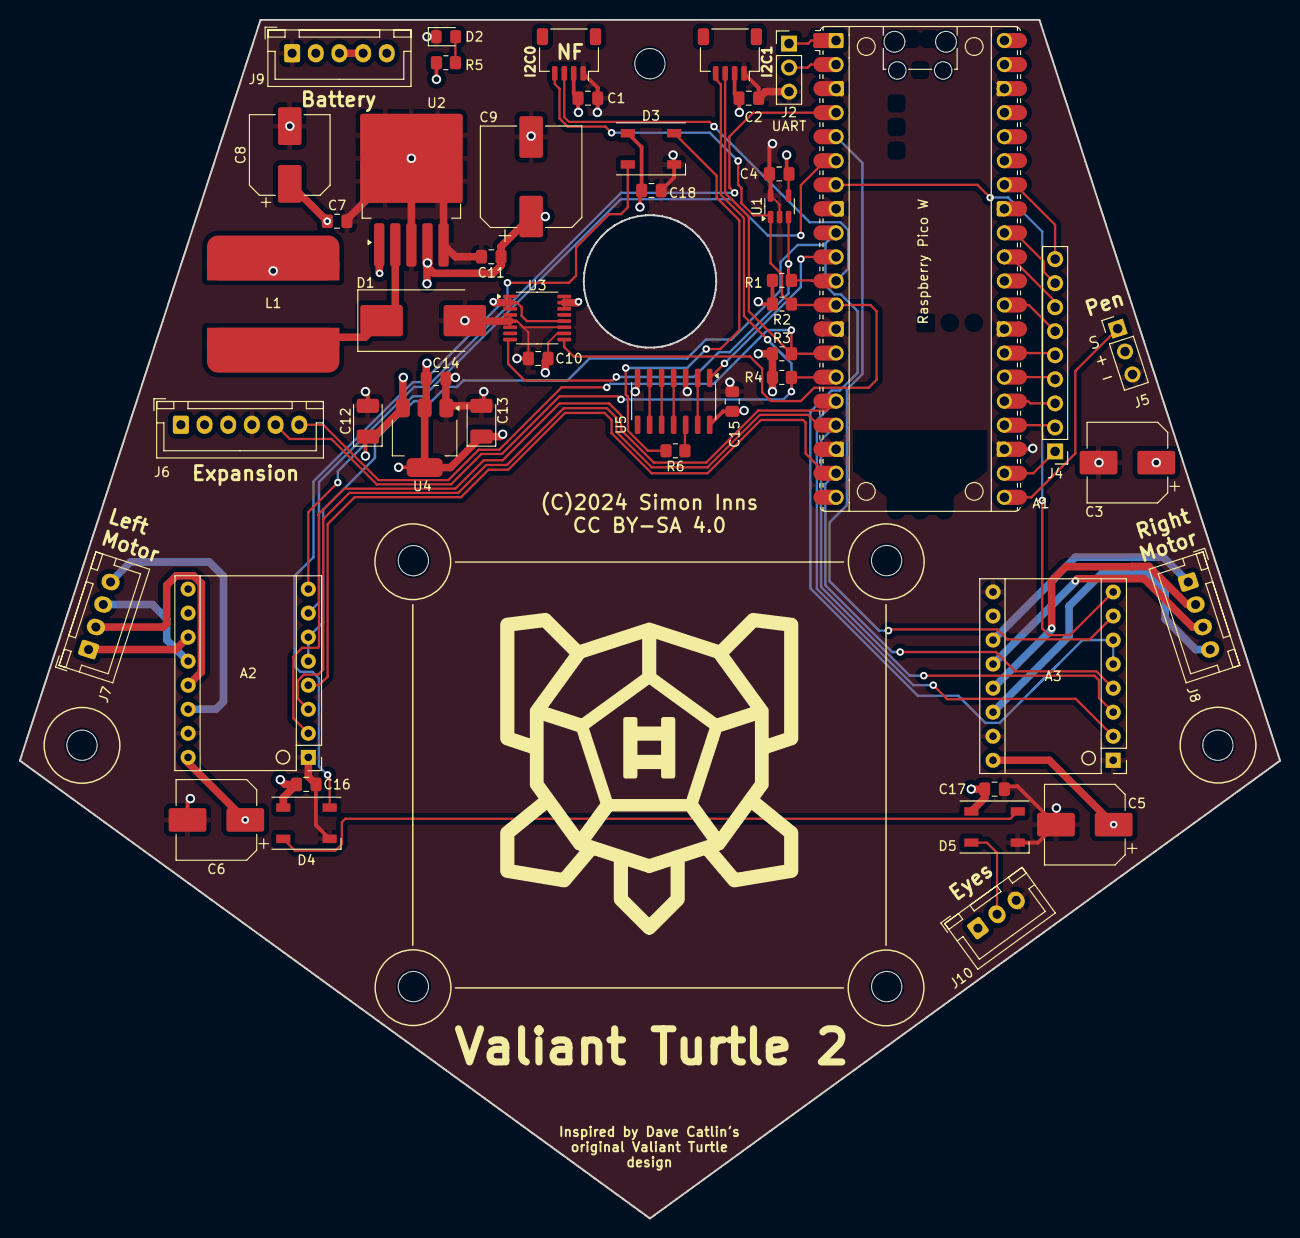
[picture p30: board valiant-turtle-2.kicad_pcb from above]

Board: 4 copper layers, 133.1 x 126.6 mm, 55 parts (0 on the bottom side), 50 nets.

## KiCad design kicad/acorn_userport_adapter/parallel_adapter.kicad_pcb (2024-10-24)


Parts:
H1, H2: MountingHole; MountingHole_3.2mm_M3
J1: BBC Micro Userport; IDC-Header_2x10_P2.54mm_Horizontal
J2: DA15_Valiant_Parallel; DSUB-15_Female_Horizontal_P2.77x2.84mm_EdgePinOffset9.90mm_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

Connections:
GND: J1.5, J1.7, J1.9, J1.11, J1.13, J1.15, J1.17, J1.19, J2.0 (PAD), J2.9, J2.10
unnamed: J1.2, J2.14
unnamed: J1.4, J2.15
unnamed: J1.6, J2.1
unnamed: J1.8, J2.2
unnamed: J1.10, J2.3
unnamed: J1.12, J2.4
unnamed: J1.14, J2.5
unnamed: J1.16, J2.6
unnamed: J1.18, J2.7
unnamed: J1.20, J2.8


Board: 2 copper layers, 39.2 x 32.0 mm, 4 parts (0 on the bottom side), 11 nets.

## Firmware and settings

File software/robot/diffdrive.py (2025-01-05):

#************************************************************************ 
#
#   diffdrive.py
#
#   Differential Drive Motor Control
#   Valiant Turtle 2 - Robot firmware
#   Copyright (C) 2024 Simon Inns
#
#   This file is part of Valiant Turtle 2
#
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
#   Email: simon.inns@gmail.com
#
#************************************************************************

import picolog
from drv8825 import Drv8825
from stepper import Stepper

from machine import Pin
import math
import time

class DiffDrive:
    def __init__(self, drv8825_enable_gpio: int, drv8825_m0_gpio :int, drv8825_m1_gpio :int, drv8825_m2_gpio :int, left_step_gpio :int, left_direction_gpio :int, right_step_gpio :int, right_direction_gpio :int):
        # Configure the DRV8825 control GPIOs
        self._drv8825_enable_pin = Pin(drv8825_enable_gpio, Pin.OUT)
        self._drv8825_m0_pin = Pin(drv8825_m0_gpio, Pin.OUT)
        self._drv8825_m1_pin = Pin(drv8825_m1_gpio, Pin.OUT)
        self._drv8825_m2_pin = Pin(drv8825_m2_gpio, Pin.OUT)

        # Create the DRV8825 instance (The DRV8825 driver is shared between the two stepper motors
        # as the enable line and microstepping mode pins are shared)
        self._steps_per_revolution = 800
        self._drv8825 = Drv8825(self._drv8825_enable_pin, self._drv8825_m0_pin, self._drv8825_m1_pin, self._drv8825_m2_pin)
        self._drv8825.set_steps_per_revolution(self._steps_per_revolution)
        self._drv8825.set_enable(False)

        # Configure the stepper control GPIOs
        self._left_step_pin = Pin(left_step_gpio, Pin.OUT)
        self._left_direction_pin = Pin(left_direction_gpio, Pin.OUT)
        self._right_step_pin = Pin(right_step_gpio, Pin.OUT)
        self._right_direction_pin = Pin(right_direction_gpio, Pin.OUT)

        # Create the stepper motor instances
        self._left_stepper = Stepper(self._drv8825, self._left_step_pin, self._left_direction_pin, True)
        self._left_stepper.set_direction_forwards()
        self._right_stepper = Stepper(self._drv8825, self._right_step_pin, self._right_direction_pin, False)
        self._right_stepper.set_direction_forwards()

        # Default linear velocity
        self._linear_target_speed_umps = 200000 # um per second
        self._linear_acceleration_umpss = 4000 # um per second per second

        # Default rotational velocity
        self._rotational_target_speed_umps = 100000 # um per second
        self._rotational_acceleration_umpss = 4000 # um per second per second

        # Default wheel diameter and axel distance
        self._wheel_diameter_um = 55530
        self._axel_distance_um = 224000

        # Default wheel and axel calibration
        self._wheel_calibration_um = 0 # micrometers
        self._axel_calibration_um = 0 # micrometers

        # Value of pi
        self._pi = 3.14159265359

        # Current position in Cartesian coordinates
        self._x_pos = 0
        self._y_pos = 0

        # Current heading in radians (common to both polar and Cartesian coordinates)
        self._heading_radians = 0

    def set_enable(self, enable: bool):
        """Enable or disable the motor driver"""
        self._drv8825.set_enable(enable)

    @property
    def is_enabled(self):
        """Returns True if the motor driver is enabled"""
        return self._drv8825.is_enabled
    
    @property
    def is_moving(self):
        """Returns True if the motors are moving"""
        return self._left_stepper.is_busy
    
    def set_wheel_calibration(self, value: int):
        """Set the wheel calibration in micrometers"""
        self._wheel_calibration_um = value

    def get_wheel_calibration(self) -> int:
        """Get the wheel calibration in micrometers"""
        return self._wheel_calibration_um

    def set_axel_calibration(self, value: int):
        """Set the axel calibration in micrometers"""
        self._axel_calibration_um = value

    def get_axel_calibration(self) -> int:
        """Get the axel calibration in micrometers"""
        return self._axel_calibration_um
    
    def drive_forward(self, distance_um: float):
        """Linear motion forwards"""
        self.__forward(distance_um)

        # Update the cartesian position, heading is self._heading_radians
        self._x_pos += distance_um * math.cos(self._heading_radians)
        self._y_pos += distance_um * math.sin(self._heading_radians)

        # Round the Cartesian position to 2 decimal places
        self._x_pos = round(self._x_pos, 2)
        self._y_pos = round(self._y_pos, 2)

    def drive_backward(self, distance_um: float):
        """Linear motion backwards"""
        self.__backward(distance_um)

        # Update the cartesian position, heading is self._heading_radians
        self._x_pos -= distance_um * math.cos(self._heading_radians)
        self._y_pos -= distance_um * math.sin(self._heading_radians)

        # Round the Cartesian position to 2 decimal places
        self._x_pos = round(self._x_pos, 2)
        self._y_pos = round(self._y_pos, 2)

    def turn_left(self, degrees: float):
        """Rotational motion to the left"""
        self.__left(math.radians(degrees))
        
        # Update the heading
        self._heading_radians += math.radians(degrees)

    def turn_right(self, degrees: float):
        """Rotational motion to the right"""
        self.__right(math.radians(degrees))

        # Update the heading
        self._heading_radians -= math.radians(degrees)

    def circle(self, radius_um: float, extent_degrees: float):
        """Move in a circle"""
        self.__circle(radius_um, math.radians(extent_degrees))

        # Update the Cartesian position and heading
        arc_center_x = self._x_pos - radius_um * math.sin(self._heading_radians)
        arc_center_y = self._y_pos + radius_um * math.cos(self._heading_radians)

        new_heading_radians = self._heading_radians + math.radians(extent_degrees)

        self._x_pos = arc_center_x + radius_um * math.sin(new_heading_radians)
        self._y_pos = arc_center_y - radius_um * math.cos(new_heading_radians)

        self._heading_radians = new_heading_radians

    def __forward(self, distance_um: float):
        """Linear motion forwards"""
        if distance_um <= 0:
            picolog.debug(f"DiffDrive::__forward - Distance in um must be greater than zero")
            return
        self.__configure_linear_velocity()
        self._left_stepper.set_direction_forwards()
        self._right_stepper.set_direction_forwards()
        picolog.debug(f"DiffDrive::__forward - Moving {distance_um} um using {self.__um_to_steps(distance_um)} steps")
        self._left_stepper.move(self.__um_to_steps(distance_um))
        self._right_stepper.move(self.__um_to_steps(distance_um))

    def __backward(self, distance_um: float):
        """Linear motion backwards"""
        if distance_um <= 0:
            picolog.debug(f"DiffDrive::__backward - Distance in um must be greater than zero")
            return
        self.__configure_linear_velocity()
        self._left_stepper.set_direction_backwards()
        self._right_stepper.set_direction_backwards()
        picolog.debug(f"DiffDrive::__backward - Moving {distance_um} um using {self.__um_to_steps(distance_um)} steps")
        self._left_stepper.move(self.__um_to_steps(distance_um))
        self._right_stepper.move(self.__um_to_steps(distance_um))

    def __left(self, radians: float):
        """Rotational motion to the left"""
        if radians <= 0:
            picolog.debug(f"DiffDrive::__left - Radians must be greater than zero")
            return
        
        if self.__radians_to_steps(radians) == 0:
            picolog.debug(f"DiffDrive::__left - Results in zero steps - not moving")
            return

        self.__configure_rotational_velocity()
        self._left_stepper.set_direction_left()
        self._right_stepper.set_direction_left()
        picolog.debug(f"DiffDrive::__left - Turning left {radians} radians using {self.__radians_to_steps(radians)} steps")
        self._left_stepper.move(self.__radians_to_steps(radians))
        self._right_stepper.move(self.__radians_to_steps(radians))

    def __right(self, radians: float):
        """Rotational motion to the right"""
        if radians <= 0:
            picolog.debug(f"DiffDrive::__right - Radians must be greater than zero")
            return
        
        if self.__radians_to_steps(radians) == 0:
            picolog.debug(f"DiffDrive::__right - Results in zero steps - not moving")
            return

        self.__configure_rotational_velocity()
        self._left_stepper.set_direction_right()
        self._right_stepper.set_direction_right()
        picolog.debug(f"DiffDrive::__right - Turning right {radians} radians using {self.__radians_to_steps(radians)} steps")
        self._left_stepper.move(self.__radians_to_steps(radians))
        self._right_stepper.move(self.__radians_to_steps(radians))

    def __circle(self, radius_um: float, extent_radians: float):
        """Move in a circle of the specified radius and extent."""

        # Ensure the radius is not zero
        if radius_um == 0:
            picolog.debug(f"DiffDrive::__circle - Radius must be non-zero")
            return
        
        # Ensure the extent is not zero
        if extent_radians == 0:
            picolog.debug(f"DiffDrive::__circle - Extent must be non-zero")
            return

        # Ensure that the absolute radius is greater than the half the axel distance
        if abs(radius_um) >= ((self._axel_distance_um + self._axel_calibration_um) / 2):
            self.__circle_big(radius_um, extent_radians)
        else:
            self.__circle_small(radius_um, extent_radians)
            return
        
    def __circle_big(self, radius_um: float, extent_radians: float):
        """Move the fulcrum of the wheel axle in a circle of the specified radius and extent (when the radius is equal or greater to the half the wheel axle distance)."""
        if abs(radius_um) < ((self._axel_distance_um + self._axel_calibration_um) / 2):
            picolog.debug(f"DiffDrive::__circle_big - Radius must be greater than or equal to the axel distance")
            return
        
        picolog.debug(f"DiffDrive::__circle_big - Moving in a circle with radius {radius_um} um and extent {math.degrees(extent_radians)} degrees")
        # If the radius is positive the outer wheel is the left wheel
        if radius_um > 0:
            outer_stepper = self._left_stepper
            inner_stepper = self._right_stepper
            picolog.debug(f"DiffDrive::__circle_big - Moving in a circle to the left, left motor is outer and right motor is inner")
        else:
            outer_stepper = self._right_stepper
            inner_stepper = self._left_stepper
            picolog.debug(f"DiffDrive::__circle_big - Moving in a circle to the right, right motor is outer and left motor is inner")

        # Calculate the outer and inner wheel distances
        outer_distance = abs(radius_um) * (extent_radians * 2)
        inner_distance = (abs(radius_um) - (self._axel_distance_um / 2)) * (extent_radians * 2)

        # Set the target speed and acceleration of the outer wheel to the maximum allowed
        self.__configure_rotational_velocity()
        outer_stepper.set_target_speed_sps(self.__um_to_steps(self._rotational_target_speed_umps))
        outer_stepper.set_acceleration_spsps(self.__um_to_steps(self._rotational_acceleration_umpss))

        # Calculate the inner wheel speed and acceleration to match the movement time of the outer wheel
        inner_speed = (inner_distance / outer_distance) * self._rotational_target_speed_umps
        inner_acceleration = (inner_distance / outer_distance) * self._rotational_acceleration_umpss

        # Set the target speed and acceleration of the inner wheel
        inner_stepper.set_target_speed_sps(self.__um_to_steps(inner_speed))
        inner_stepper.set_acceleration_spsps(self.__um_to_steps(inner_acceleration))

        # If extent is positive, both wheels move forwards
        if extent_radians > 0:
            outer_stepper.set_direction_forwards()
            inner_stepper.set_direction_forwards()
        else:
            outer_stepper.set_direction_backwards()
            inner_stepper.set_direction_backwards()

        # Ensure steps are positive
        outer_distance = abs(outer_distance)
        inner_distance = abs(inner_distance)

        # Move the outer and inner wheels
        outer_stepper.move(self.__um_to_steps(outer_distance))
        inner_stepper.move(self.__um_to_steps(inner_distance))

    def __circle_small(self, radius_um: float, extent_radians: float):
        """Move the fulcrum of the wheel axle in a circle of the specified radius and extent
        (when the radius describes the path of the midpoint between the wheels and is smaller 
        than half the axle distance, requiring opposite rotation for the inner wheel)."""

        if abs(radius_um) >= ((self._axel_distance_um  + self._axel_calibration_um) / 2):
            picolog.debug(f"DiffDrive::__circle_small - Radius must be smaller than half the axle distance")
            return

        picolog.debug(f"DiffDrive::__circle_small - Moving in a circle with radius {radius_um} um and extent {math.degrees(extent_radians)} degrees")

        # Determine which wheel is inner and which is outer
        if radius_um > 0:
            outer_stepper = self._left_stepper
            inner_stepper = self._right_stepper
            picolog.debug(f"DiffDrive::__circle_small - Moving in a tight circle to the left, left motor is outer and right motor is inner")
        else:
            outer_stepper = self._right_stepper
            inner_stepper = self._left_stepper
            picolog.debug(f"DiffDrive::__circle_small - Moving in a tight circle to the right, right motor is outer and left motor is inner")

        # Calculate the actual radii for the inner and outer wheels
        outer_radius = abs(radius_um) + ((self._axel_distance_um + self._axel_calibration_um) / 2)
        inner_radius = abs(radius_um) - ((self._axel_distance_um + self._axel_calibration_um) / 2)

        # Calculate the distances traveled by each wheel
        outer_distance = outer_radius * abs(extent_radians)
        inner_distance = inner_radius * abs(extent_radians)

        # Set the target speed and acceleration for the outer wheel
        self.__configure_rotational_velocity()
        picolog.debug(f"DiffDrive::__circle_small - Setting outer stepper target speed to {self._rotational_target_speed_umps} um/s and acceleration to {self._rotational_acceleration_umpss} um/s^2")
        outer_stepper.set_target_speed_sps(self.__um_to_steps(self._rotational_target_speed_umps))
        outer_stepper.set_acceleration_spsps(self.__um_to_steps(self._rotational_acceleration_umpss))

        # Calculate the inner wheel speed and acceleration to match the movement time of the outer wheel
        inner_speed = abs((inner_distance / outer_distance) * self._rotational_target_speed_umps)
        inner_acceleration = abs((inner_distance / outer_distance) * self._rotational_acceleration_umpss)

        # Set the target speed and acceleration for the inner wheel
        picolog.debug(f"DiffDrive::__circle_small - Setting inner stepper target speed to {inner_speed} um/s and acceleration to {inner_acceleration} um/s^2")
        inner_stepper.set_target_speed_sps(self.__um_to_steps(inner_speed))
        inner_stepper.set_acceleration_spsps(self.__um_to_steps(inner_acceleration))

        # Handle wheel direction: inner wheel rotates in the opposite direction
        if extent_radians > 0:
            outer_stepper.set_direction_forwards()
            inner_stepper.set_direction_backwards()
            picolog.debug(f"DiffDrive::__circle_small - Outer wheel moves forward, inner wheel moves backward")
        else:
            outer_stepper.set_direction_backwards()
            inner_stepper.set_direction_forwards()
            picolog.debug(f"DiffDrive::__circle_small - Outer wheel moves backward, inner wheel moves forward")

        # Move the outer and inner wheels
        outer_stepper.move(self.__um_to_steps(abs(outer_distance)))
        inner_stepper.move(self.__um_to_steps(abs(inner_distance)))

    def set_heading(self, degrees: float):
        """Set the heading in degrees"""
        degrees = degrees % 360

        current_heading_degrees = math.degrees(self._heading_radians)
        if math.isclose(current_heading_degrees, degrees, abs_tol=1e-2):
            picolog.debug(f"DiffDrive::set_heading - Already at required heading ({degrees}°)")
            return

        # Convert degrees to radians
        target_radians = math.radians(degrees)

        # Set the heading
        self.__set_heading(target_radians)

    def __set_heading(self, target_radians: float):
        # Normalize the angle difference to the range [-π, π]
        def normalize_angle(angle):
            return (angle + math.pi) % (2 * math.pi) - math.pi

        angle_difference = normalize_angle(target_radians - self._heading_radians)

        # Determine turning direction
        if angle_difference > 0:
            picolog.debug(f"DiffDrive::__set_heading - Turning left by {math.degrees(angle_difference):.2f} degrees")
            self.turn_left(math.degrees(angle_difference))
        elif angle_difference < 0:
            picolog.debug(f"DiffDrive::__set_heading - Turning right by {math.degrees(-angle_difference):.2f} degrees")
            self.turn_right(math.degrees(-angle_difference))

        # Update the heading to the target value
        self._heading_radians = target_radians

    def get_heading(self) -> float:
        """Get the heading in degrees"""
        heading_degrees = round(math.degrees(self._heading_radians), 2) % 360
        return heading_degrees

    def set_cartesian_x_position(self, x: float):
        """Move to the specified x-coordinate"""
        self.set_cartesian_position(x, self._y_pos, False)

    def set_cartesian_y_position(self, y: float):
        """Move to the specified y-coordinate"""
        self.set_cartesian_position(self._x_pos, y, False)

    def turn_towards_cartesian_point(self, x: float, y: float):
        """Turn towards the specified Cartesian point"""
        self.set_cartesian_position(x, y, True)

    def set_cartesian_position(self, x: float, y: float, turn_only: bool = False):
        """Move to the specified x and y coordinates in one motion."""
        if x == self._x_pos and y == self._y_pos:
            picolog.debug("Already at the required position.")
            return

        # Store the current heading
        current_heading = self._heading_radians

        # Calculate the target angle and distance
        delta_x = x - self._x_pos
        delta_y = y - self._y_pos
        target_angle = math.atan2(delta_y, delta_x)
        distance = math.sqrt(delta_x**2 + delta_y**2)

        # Normalize angles to [-pi, pi]
        angle_diff = (target_angle - self._heading_radians + math.pi) % (2 * math.pi) - math.pi

        # Determine the turning direction based on the angle difference
        # Note: Always turn towards the position (facing forwards) if turn_only is True
        if abs(angle_diff) > math.pi / 2 and not turn_only: 
            # Backward movement
            turn_angle = math.pi - abs(angle_diff)
            turn_angle *= -1 if angle_diff > 0 else 1

            if angle_diff > 0:
                self.__right(abs(turn_angle))
            else:
                self.__left(abs(turn_angle))

            self._heading_radians = (self._heading_radians + turn_angle) % (2 * math.pi)

            picolog.debug("DiffDrive::set_cartesian_position - Waiting for turn to complete (backward).")
            while self._left_stepper.is_busy or self._right_stepper.is_busy:
                time.sleep(0.2)

            if not turn_only:
                self.drive_backward(distance)

                picolog.debug("DiffDrive::set_cartesian_position - Waiting for movement to complete (backward).")
                while self._left_stepper.is_busy or self._right_stepper.is_busy:
                    time.sleep(0.2)

                # Restore the original heading
                self.__set_heading(current_heading)                
        else:
            # Forward movement
            if angle_diff > 0:
                self.__left(angle_diff)
            else:
                self.__right(-angle_diff)

            self._heading_radians = (self._heading_radians + angle_diff) % (2 * math.pi)

            picolog.debug("DiffDrive::set_cartesian_position - Waiting for turn to complete (forward).")
            while self._left_stepper.is_busy or self._right_stepper.is_busy:
                time.sleep(0.2)

            if not turn_only:
                self.drive_forward(distance)

                picolog.debug("DiffDrive::set_cartesian_position - Waiting for movement to complete (forward).")
                while self._left_stepper.is_busy or self._right_stepper.is_busy:
                    time.sleep(0.2)

                # Restore the original heading
                self.__set_heading(current_heading) 

    def get_cartesian_position(self) -> tuple:
        """Get the Cartesian x and y position"""
        return round(self._x_pos, 2), round(self._y_pos, 2)

    def reset_origin(self):
        """Reset the Cartesian origin and heading to the current position"""
        picolog.debug(f"DiffDrive::reset_origin - Resetting origin and heading")
        self._x_pos = 0
        self._y_pos = 0
        self._heading_radians = 0
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

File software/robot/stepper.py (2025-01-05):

#************************************************************************ 
#
#   stepper.py
#
#   Stepper motor control (via DRV8825)
#   Valiant Turtle 2 - Robot firmware
#   Copyright (C) 2024 Simon Inns
#
#   This file is part of Valiant Turtle 2
#
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
#   Email: simon.inns@gmail.com
#
#************************************************************************

import picolog
from pulse_generator import PulseGenerator
from drv8825 import Drv8825

from machine import Pin

class Stepper:
    _sm_counter = 0 # Keep track of the next free state-machine
    test_only = False # Set to True to test the acceleration sequence without moving the stepper

    def __init__(self, drv8825: Drv8825, step_pin: Pin, direction_pin: Pin, is_left: bool):
        self.pio = 0

        # Configure the stepper motor direction
        self._is_left = is_left
        self._direction_pin = direction_pin
        self.set_direction_forwards()

        # Stepper busy flag
        self._is_busy = False
        self._direction = True # True = forwards, False = backwards

        # Stepper motion parameters (in steps per interval)
        self._target_speed_spi = 1
        self._acceleration_spi = 1
        self._steps_remaining = 0
        self._current_speed_spi = 1

        # Tracking parameters
        self._acceleration_steps = 0
        self._running_steps = 0
        self._track_actual_steps = 0

        # The number of speed re-calculations per second
        self._intervals_per_second = 16

        # Temporary acceleration and target speed values in case
        # we need to adjust them for a single move
        self._actual_acceleration_spi = self._acceleration_spi
        self._actual_target_speed_spi = self._target_speed_spi

        # Ensure we have a free state-machine
        if Stepper._sm_counter < 4:
            if self._is_left:
                picolog.debug(f"Stepper::__init__ - Left stepper pulse generator using PIO {self.pio} SM {Stepper._sm_counter}")
            else:
                picolog.debug(f"Stepper::__init__ - Right stepper pulse generator using PIO {self.pio} SM {Stepper._sm_counter}")
        else:
            raise RuntimeError("Stepper::__init__ - No more state machines available!")

        # Initialise the pulse generator on PIO 1
        # Note: This controls the step GPIO
        self._state_machine = Stepper._sm_counter
        Stepper._sm_counter += 1
        self.pulse_generator = PulseGenerator(self.pio, self._state_machine, step_pin)
        
        # Set up the pulse generator callback
        self.pulse_generator.callback_subscribe(self.callback)

    @property
    def is_busy(self):
        return self._is_busy
    
    @property
    def direction(self):
        return self._direction
    
    def set_direction_forwards(self):
        if self._is_left:
            self._direction_pin.value(1)
        else:
            self._direction_pin.value(0)
        self._direction = True

    def set_direction_backwards(self):
        if self._is_left:
            self._direction_pin.value(0)
        else:
            self._direction_pin.value(1)
        self._direction = False

    def set_direction_left(self):
        if self._is_left:
            self._direction_pin.value(1)
        else:
            self._direction_pin.value(1)
        if self._is_left: 
            self._direction = True
        else:
            self._direction = False

    def set_direction_right(self):
        if self._is_left:
            self._direction_pin.value(0)
        else:
            self._direction_pin.value(0)
        if self._is_left: 
            self._direction = False
        else:
            self._direction = True

    def set_acceleration_spsps(self, acceleration: float):
        """Set the acceleration in steps per second per second"""
        if acceleration < 1:
            raise ValueError("Stepper::set_acceleration - Acceleration must be greater than 0")
        self._acceleration_spi = acceleration / self._intervals_per_second
        picolog.debug(f"Stepper::set_acceleration - Acceleration set to {acceleration} steps per second per second ({self._acceleration_spi} steps per interval per interval)")

    def set_target_speed_sps(self, target_speed: float):
        """Set the target speed in steps per second"""
        if target_speed < 1:
            raise ValueError("Stepper::set_target_speed - Speed must be greater than 0")
        self._target_speed_spi = target_speed / self._intervals_per_second
        picolog.debug(f"Stepper::set_target_speed - Target speed set to {target_speed} steps per second ({self._target_speed_spi} steps per interval)")

    def move(self, steps: float):
        # Check if the stepper is currently busy
        if self._is_busy:
            raise RuntimeError("Stepper::move - Stepper is currently busy")
        
        if (steps == 0):
            picolog.debug("Stepper::move - Steps must be greater than 0 - not moving")
            return

        # Set the stepper as busy
        self._is_busy = True

        picolog.debug(f"Stepper::move - Moving {steps} steps using {self._intervals_per_second} calculation intervals per second")
        picolog.debug(f"Stepper::move - Maximum acceleration is {self._acceleration_spi} steps per interval and target speed is {self._target_speed_spi} steps per interval")

        self._total_steps = steps
        self._steps_remaining = self._total_steps
        self._current_speed_spi = 0
        self._maximum_available_acceleration_steps = self._total_steps / 2
        one_shot = False
        self._partial_steps = 0
        self._track_actual_steps = 0

        # Save the initial acceleration and target speed in case we need to adjust them
        self._actual_acceleration_spi = self._acceleration_spi
        self._actual_target_speed_spi = self._target_speed_spi

        # Ensure that we have enough steps to accelerate
        if self._total_steps < (2 * self._actual_acceleration_spi):
            if (self._total_steps / 2) >= 1:
                self._actual_acceleration_spi = int(self._total_steps / 2)
                picolog.debug(f"Stepper::move - Adjusting acceleration to {self._actual_acceleration_spi} steps per interval")
            else:
                picolog.debug("Stepper::move - Cannot accelerate: Steps must be greater than or equal to 2")
                one_shot = True
        
        # Range check and adjust the target speed if necessary
        if (self._actual_target_speed_spi <= self._actual_acceleration_spi):
            self._actual_target_speed_spi = self._actual_acceleration_spi
            picolog.debug(f"Stepper::move - Adjusting target speed to {self._actual_target_speed_spi} steps per interval")
        
        if (self._total_steps < self._actual_target_speed_spi):
            self._actual_target_speed_spi = self._total_steps
            picolog.debug(f"Stepper::move - Adjusting target speed to {self._actual_target_speed_spi} steps per interval")
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

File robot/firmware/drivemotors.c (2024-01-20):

/************************************************************************ 

    drivemotors.c

    Valiant Turtle 2 - Raspberry Pi Pico W Firmware
    Copyright (C) 2023 Simon Inns

    This file is part of Valiant Turtle 2

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
    Email: simon.inns@gmail.com

************************************************************************/

#include <stdio.h>
#include <pico/stdlib.h>
#include <string.h>

#include "drivemotors.h"
#include "debug.h"
#include "btcomms.h"

// Globals
stepperMotor_t leftMotor;
stepperMotor_t rightMotor;

bool motorTimerCallback(repeating_timer_t *rt);
repeating_timer_t motorTimer;

void driveMotorsInitialise(void)
{
    // Initialise the drive motor control GPIOs
    gpio_init(DM_ENABLE_GPIO);
    gpio_init(DM_LSTEP_GPIO);
    gpio_init(DM_RSTEP_GPIO);
    gpio_init(DM_LDIR_GPIO);
    gpio_init(DM_RDIR_GPIO);
    gpio_init(DM_LM0_GPIO);
    gpio_init(DM_LM1_GPIO);
    gpio_init(DM_RM0_GPIO);
    gpio_init(DM_RM1_GPIO);

    // Set the drive motor control GPIO directions
    gpio_set_dir(DM_ENABLE_GPIO, GPIO_OUT);
    gpio_set_dir(DM_LSTEP_GPIO, GPIO_OUT);
    gpio_set_dir(DM_RSTEP_GPIO, GPIO_OUT);
    gpio_set_dir(DM_LDIR_GPIO, GPIO_OUT);
    gpio_set_dir(DM_RDIR_GPIO, GPIO_OUT);
    gpio_set_dir(DM_LM0_GPIO, GPIO_OUT);
    gpio_set_dir(DM_LM1_GPIO, GPIO_OUT);
    gpio_set_dir(DM_RM0_GPIO, GPIO_OUT);
    gpio_set_dir(DM_RM1_GPIO, GPIO_OUT);

    // Default values
    driveMotorsEnable(false);
    driveMotorsRunning(false);
    driveMotorSetDir(MOTOR_LEFT, MOTOR_FORWARDS);
    driveMotorSetDir(MOTOR_RIGHT, MOTOR_FORWARDS);
    driveMotorSetMaximumSpeed(MOTOR_LEFT, MOTOR_1600);
    driveMotorSetMaximumSpeed(MOTOR_RIGHT, MOTOR_1600);

    // Set remaining steps to zero
    leftMotor.steps = 0;
    rightMotor.steps = 0;
    
    // Set the initial step states to off
    leftMotor.state = 0;
    rightMotor.state = 0;

    // Set up the repeating motor update timer
    // Maximum DRV8825 frequency is 1.9us, so we need to callback every
    // 850us with a pulse at 50% duty
    if (!add_repeating_timer_us(-1900/2, motorTimerCallback, NULL, &motorTimer)) {
        debugPrintf("Drive motors: Failed to add motor update timer!\r\n");
    }
}

// Callback function for the motor pulse timer
bool motorTimerCallback(repeating_timer_t *rt)
{
    if (leftMotor.enabled && leftMotor.running) {
        // Step the left motor
        if (leftMotor.steps > 0) {
            if (leftMotor.state == 0) {
                gpio_put(DM_LSTEP_GPIO, 1);
                leftMotor.state++;
            } else {
                gpio_put(DM_LSTEP_GPIO, 0);
                leftMotor.state++;
            }

            // Reset state and decrement steps according to speed
            if (leftMotor.state > 1) {
                leftMotor.state = 0;
                switch (leftMotor.currentSpeed) {
                     case MOTOR_200: leftMotor.steps -= 8;
                        break;
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

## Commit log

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2023-11-26 Fixed shape of the upper shell
    [main.scad, shell.scad]
2023-11-27 New shell shape, might be a little small around the lower egde?
    [body.scad, main.scad, shell.scad]
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2023-11-28 Fixed shell and body positioning
    [body.scad, isoahedron.scad, shell.scad]
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2023-11-30 More fixes to the wheel covers and back edge of the shell
    [shell.scad]
2023-12-02 Split shell into sub modules, fixes to wheel arches
    [main.scad, shell_bottom.scad, shell_top.scad]
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2023-12-02 Fixed wheel arches and added point documentation and pictures to the repo
    [shell_bottom.scad, shell_top.scad]
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2023-12-03 Started work on the actual body design and included a point naming guide for the body shape
    [body.scad, shell_bottom.scad]
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2023-12-10 Added motor mounts, wheels and associated stuff - split into multiple modules
    [body.scad, head.scad, main.scad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]
2023-12-10 Fixed some minor issues and added threaded inserts to the lower shell
    [body.scad, head.scad, motor_mounts.scad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]
2023-12-10 Moved the back of the lower shell to cover the motor bay cutouts correctly
    [shell_bottom.scad]
2023-12-10 Added printing modes for most parts, added LED eyes + some clean up
    [body.scad, head.scad, leds.scad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]
2023-12-11 Added head cover, improved LED placement and seperated caster ball base for printing
    [body.scad, head.scad, head_cover.scad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]
2023-12-11 Fixed some colours to tidy up look
    [motor_mounts.scad, pcb.scad]
2023-12-12 Added support enforcers and cleaned up join between upper and lower shell
    [body.scad, body.stl, body_se.stl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]
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2023-12-14 Changed motor bay and body design to reduce printing complexity and supports
    [body.scad, main.scad, motor_bay.scad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]
2023-12-15 Added some strength to the front of the body to prevent the head flexing
    [body.scad, body.stl, body_se.stl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]
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2023-12-15 Corrected motor mount print
    [motor_mount.stl, motor_mounts.scad]
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2023-12-15 Changed body and motor mounts/bay to allow bigger NEMA 17 motors with 24mm shafts
    [body.scad, body.stl, motor_bay.scad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]
2023-12-15 Redesigned wheels and motor bay for big and small NEMA 17 motors with 20-24mm shafts
    [main.scad, motor_bay.scad, motor_bay.stl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]
2023-12-15 Fixed rotational axis guide according to the new wheel positions
    [wheels.scad]
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2023-12-16 Fixed front and back PCB mounts for new split body profile
    [main.scad, pcb.scad]
2023-12-16 Made the back PCB mount look a little nicer - generated STLs for the mounts
    [pcb.scad, pcb_mount_back.stl, pcb_mount_front.stl]
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2023-12-16 Fixed issue with body shape and added body screws
    [body.scad, body_left.stl, body_right.stl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]
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2023-12-16 Changed wheel arches back to original shape and moved the joiner to the top shell module
    [shell_bottom.scad, shell_top.scad]
2023-12-16 Fixed a clearance issue between the wheels and the motor bay
    [body.scad, body_left.stl, body_right.stl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]
2023-12-16 Made the wheel shaft hole a little bigger as it was too tight
    [wheel.stl, wheels.scad]
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2023-12-16 Fixed screw length issue with motor bay to body mounting screws
    [motor_bay.scad, motor_bay.stl]
2023-12-17 Motor bay screw position, rotated body print position, bevelled pen hole, fixed head not fitting issue, additional wheel clearance vs body shape
    [body.scad, body_left.stl, body_right.stl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]
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2023-12-17 Fixed servo mount printing position
    [pen_holder_base.stl, pen_holder_top_medium.stl, servo_holder.scad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]
2023-12-18 Made servo mount holes a bit bigger and removed all old STL files
    [body_left.stl, body_right.stl, head.stl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]
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2023-12-18 Redesigned shell into two printable parts
    [body_left.stl, body_right.stl, shell_bottom.scad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]
2023-12-18 Fixed some minor issues with the motor bays for better printing
    [motor_bay.scad, motor_bay.stl]
2023-12-18 Added a cap for the pen holder to stop the pen from drying out when not in use
    [head.stl, main.scad, motor_bay.scad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]
2023-12-18 Redesigned head and head cover after head part broke after printing in PETG. Removed need for supports
    [head.scad, head.stl, head_cover.scad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]
2023-12-18 Removed the screw recess on the front of the motor mounts for cleaner printing
    [motor_mounts.scad, motor_mounts.stl]
2023-12-19 Fixed head height issue and redesigned head cover (shell now wrong)
    [head.scad, head.stl, head_cover.scad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]
2023-12-19 Fixed shell to match new head dimensions (and re-added missing bit of head into code)
    [head.scad, shell_bottom.scad, shell_top.scad]
2023-12-19 Redesigned wheel to be a bit thicker and better to print
    [pcb_mount_back.stl, pcb_mount_front.stl, wheel.stl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]
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2023-12-20 Made screw recess deeper for front and back PCB mounts to prevent screws from hitting the plastic when screwed through a 1.4mm PCB
    [pcb.scad, pcb_mount_back.stl, pcb_mount_front.stl]
2023-12-21 Changed wheel design to stop them wobbling
    [main.scad, shell_bottom.scad, shell_bottom.stl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]
2023-12-21 Redesigned the shell structure and created a lid for it
    [main.scad, shell.scad, shell.stl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]
2023-12-21 Changed wheel arch design for better printing and more clearance
    [shell.scad]
2023-12-21 Added support to the shell and corrected the front body mount for printing
    [main.scad, shell.scad, shell.stl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]
2023-12-21 Redesign of pen holder
    [main.scad, motor_mounts.scad, pen_holder_base.scad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]
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2023-12-22 Fixes to shell wheel arch and lid after a test print
    [shell.scad, shell.stl, shell_lid.stl]
2023-12-22 Updated body for new pen holder design and added logo to a front flipper
    [body.scad, body_left.stl, body_right.stl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]
2023-12-22 Fixed mistake with the pen hole key design and regenerated body STLs for test printing
    [body.scad, body_left.stl, body_right.stl]
2023-12-22 Corrected mistake in top shell
    [shell.scad]
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2023-12-23 Changed pen holder dimensions for easier fit and corrected logotype display position
    [body_right.stl, logotype.scad, main.scad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]
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2023-12-24 Change servo mount to add pen mech support to prevent wobble of pen
    [body.scad, main.scad, pen.stl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]
2023-12-24 Fixed servo holder design for more stability
    [pcb.stl, servo_holder.scad, servo_mount.stl]
2023-12-24 Added some alignment tabs to the motor mounts to keep the shell in the right place
    [motor_mounts.scad, motor_mounts.stl]
2023-12-24 Fixed servo mount to make it hold the shell in position better
    [motor_mounts.scad, servo_holder.scad, servo_mount.stl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]
2023-12-24 added back in the missing shell pieces
    [shell.scad]
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2023-12-29 Small fixes to schematic and added I2C Qwiic
    [valiant-turtle-2.kicad_sch]
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2023-12-30 Corrected schematic and included basic test code for servos and steppers
    [valiant-turtle-2.kicad_sch]
2023-12-30 Fixed stepper driver test
    [drivemotors.c]
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2023-12-30 Added 5V supplies to schematic and added basic battery holder test design to the OpenSCAD files
    [batt_mon.kicad_sch, battery.scad, battery_holder.stl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]
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2023-12-31 Fitting in the battery holder to the body and moving the screws around to make it all fit
    [battery.scad, body.scad, main.scad]
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2024-01-01 Changed design of head for better LED cable access (inc head cover)
    [battery.scad, body_left.stl, body_right.stl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]
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2024-01-01 Made the battery cover slightly smaller as it was getting stuck
    [battery.scad, battery_cover.stl]
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2024-01-02 Rolled back on the printable led holders (didn't work) - added body supports to front flippers
    [body.scad, body_left.stl, body_right.stl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]
2024-01-02 Added black dot to top of shell... no one knows what it's for... but it's there none the less
    [main.scad, shell.scad]
2024-01-03 Fixed channels in the battery holder
    [battery.scad, battery_holder.stl]
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2024-01-05 Changed schematic to get PWM channels correct. General updates from ERC test.
    [power_supply.kicad_sch, rgb_led.kicad_sch, stepperdriver.kicad_sch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]
2024-01-05 Fixed code according to new schematic - added RGB LED test code to CLI
    [command.c, drivemotors.h, leds.c]
2024-01-05 Changed power switch to a connector so it can be mounted off-board
    [power_supply.kicad_sch]
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2024-01-06 Moved pico to the right-side of the board since it puts more connectors on the left closer to where they should be
    [valiant-turtle-2.kicad_pcb]
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2024-01-06 Fixed silkscreen positions
    [valiant-turtle-2.kicad_pcb]
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2024-01-07 Fixed some minor rendering problems and improved the rendering of screws to make it all faster
    [battery.scad, motor_bay.stl, servo_holder.scad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]
2024-01-07 Added a small hole to the back of the head cover to allow the ball bearing to be pushed out with a 2mm hex key
    [head.stl, head_cover.scad]
2024-01-08 Corrected main.scad and regenerated all STL files
    [battery_cover.stl, head_cover.stl, main.scad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]
2024-01-09 Made shell 1mm thick instead of 2mm to increase the transparency when printed
    [pen_holder_cap.stl, shell.scad, shell.stl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]
2024-01-09 Fixed the shell lid
    [shell.scad]
2024-01-09 Fixed shell dot
    [shell.scad]
2024-01-09 Added some support to the base of the shell and added some chamfer to the top of the head
    [head.scad, head.stl, shell.scad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]
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2024-01-09 Modified wheel hub to allow threaded insert to be inserted more easily
    [wheel.stl, wheels.scad]
2024-01-11 Fixed lid design to actually fit the shell (hopefully)
    [shell.scad, shell.stl, shell_lid.stl]
2024-01-11 Changed lid lip a little for tight fit to shell
    [shell.scad, shell_dot.stl, shell_lid.stl]
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2024-01-12 Reversed Qwiic connector and fixed RGB led code bug
    [valiant-turtle-2.kicad_sch]
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2024-01-12 Reshaped front of head slightly to try and avoid colapsing point due to hard turn
    [head.scad, head.stl]
2024-01-12 Added initial mock up of OLED display and buttons to the PCB in OpenSCAD
    [pcb.scad]
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2024-01-12 Corrected a couple of small issues
    [display_mount.scad, main.scad, pcb.scad]
2024-01-13 Redesigned servo holder - wider switch recess and fix for issue #4
    [servo_holder.scad, servo_holder.stl]
2024-01-13 Moved all robot related files to a robot sub-directory to allow control box to be added later
    [battery.scad, battery_cover.stl, body.scad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]
2024-01-13 Added BT library - all compiles, but probably doesn't work yet
    [wheel.stl]
2024-01-14 Fixed M3 hole size for issue #9
    [body.scad, motor_mounts.scad]
2024-01-14 Fixed button hole size for issue #10
    [display_mount.scad]
2024-01-15 First attempt at an output buffer for bluetooth - doesn't quite work yet :)
    [command.c]
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2024-01-15 Fixed annoying compiler warning and changed debug function name for clarity
    [command.c]
2024-01-15 Fixed bluetooth console correctly and added IIC command output to BT
    [command.c]
2024-01-15 Removed old cli.h and .c files as they are no longer required
    [command.c]
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2024-01-15 Improved motor control functions, but timer isn't really working correctly yet
    [command.c, drivemotors.c, drivemotors.h]
2024-01-16 Corrected motor control and removed display timer (polling instead)
    [drivemotors.c]
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2024-01-18 New test design of shell - also added handles to pen holder to help inserting pens when the PCB is fitted
    [pen_holder_top.scad, pen_holder_top_large.stl, pen_holder_top_medium.stl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]
2024-01-19 Revert the changes to the shell
    [shell.scad]
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2024-01-20 Prevented change of motor direction when motors are running - prevented setting motors to running when not enabled
    [command.c, drivemotors.c, drivemotors.h]
2024-08-26 Moved old firmware to another directory. Upgraded kicad from 7 to 8
    [mounting.kicad_sch, power_supply.kicad_sch, rgb_led.kicad_sch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]
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2024-09-02 Changed wheel design to be wider and use 2 o-rings for better grip. Also added spacer to ensure that the distance between the hub and the motor is even on both sides
    [wheel.stl, wheels.scad]
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2024-09-05 Correction to turning circle diameter in SCAD
    [head_cover.scad, wheels.scad]
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2024-09-05 Fixed minor issue with the calibration guide
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2024-09-06 Added tag to head and fixed threaded inserts. Moved PCB to main_pcb and fixed threaded inserts also.
    [head.scad, main.scad, main_pcb.scad]
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2024-09-07 Changed servo holder to generate better clearance for battery pack
    [body.scad, servo_holder.scad]
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2024-09-11 Added ignore file to prevent STL files uploading to git
    [body_left.stl, body_right.stl, head_shell_screw_guide.stl]
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2024-09-11 Fixed battery screws for new battery design
    [battery.scad]
2024-09-11 Fixed screws and some minor text changes around support enforcers
    [main.scad, main_pcb.scad]
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2024-09-11 Fixed logotype so it correctly generates both 3D and 2D versions (including SVG)
    [logotype.scad, main.scad]
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2024-09-12 Corrections and improvements to battery upper cover after test printing
    [battery.scad]
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2024-09-14 Added a little more internal screw clearance to the battery pack body
    [battery.scad]
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2024-09-19 Fix to mistake in charger base (misaligned PCB mounts)
    [base.scad]
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2024-09-20 Changed light pipe design for easier printing and solved issue #23
    [base.scad, battery_cutout.scad, lid.scad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]
2024-09-20 Fixed issue #24 - added polarity symbols to all battery connectors
    [battery.scad, connector.scad, servo_holder.scad]
2024-09-20 Fix for issue #19
    [motor_bay.scad, shell.scad, threaded_inserts.scad]
2024-09-20 Fixed issue #28. Fixed issue #25
    [main.scad, motor_bay.scad, motor_mounts.scad]
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2024-09-20 Fix for issue #26
    [logotype.scad]
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2024-09-23 Fix for issue #31 Also included step delay calculation spreadsheet
    [PPS_to_delay_calc.ods, stand.scad]
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2024-09-24 Added some missing checks to make sure the steppers aren't reconfigured when busy
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2024-09-28 First battery clip design to replace BML SMT dual-battery holder
    [battery.scad, battery_clip.scad, main.scad]
2024-09-28 Redesigned the battery clip after some test prints. Added the clip to the STL generation script
    [battery_clip.scad]
2024-09-28 Made the battery clip a little wider and corrected some small mistakes
    [battery_clip.scad]
2024-09-28 Fixed dimensions to get battery clip on the upper batter case lid again. Moved BMS
    [battery.scad, battery_clip.scad]
2024-09-29 Added upper support to the battery clip and corrected the battery contact position
    [battery.scad, battery_clip.scad]
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2024-09-29 Fix for issue #37 - changed screws to DIN912 hex standard
    [battery.scad, body.scad, head_cover.scad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]
2024-09-29 Fixed issue with DIN912 head size. Should be 5.5 not 5.25mm
    [battery.scad, body.scad, head_cover.scad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]
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2024-10-01 Changed head and head cover for new light pipe design. Fixed small issue with battery clip screw hole diameter
    [battery_clip.scad, head.scad, head_cover.scad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]
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2024-10-03 Fixed issue #42
    [main.scad, stand.scad]
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2024-10-04 Moved Pico foorprints to submodule. Corrected schematic issues and general schematic clean up ready for PCB design
    [mounting.kicad_sch, power_supply.kicad_sch, rgb_led.kicad_sch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]
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2024-10-05 Fixed some minor errors in the silkscreen and tidied it up a bit
    [valiant-turtle-2.kicad_pcb]
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2024-10-11 redesign of head and eyes. Added mount for AUX PCB
    [aux_pcb.scad, eyes.scad, head.scad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]
2024-10-11 Missed an unsaved file in the previous push
    [aux_pcb.scad]
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2024-10-14 Added Bluetooth stack code to communicator and fixed BT COD to match between robot and communicator
    [probe1.cfg, probe2.cfg]
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2024-10-24 Fixed communicator SCAD header messages
    [ircover.scad, label.scad, main.scad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]
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2024-10-31 Swapped Communicator CTS and RTS for issue #48 and remove two 10K pull-ups for issue #47
    [parallel_interface.kicad_sch, vt2_communicator.kicad_sch]
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2024-11-02 Fixes to the parallel port implementation in communicator firmware
    [main.py, mcp23017.py, parallel_port.py]
2024-11-03 Fixes and improvements to the communicator logging function
    [ir_uart.py, log.py, main.py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]
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2024-11-04 Working eeprom code - no serialization functioning yet (pickle is broken)
    [configuration.py, eeprom.py, main.py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]
2024-11-04 Fixed header of .py files (communicator firmware) to state module purpose
    [configuration.py, eeprom.py, ir_uart.py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]
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2024-11-05 Added better LED fading control and fixed issue with steppers and ws2812s using the same PIO
    [drv8825.py, main.py, pulse_generator.py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]
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2024-11-11 Fixed led routine to use in-built micropython library instead of PIO - now there is no flicker at all
    [led_fx.py, main.py, ws2812b.py]
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2024-11-12 More structural fixes to the BLE code - but the central/peripherial is the wrong way round...
    [ble_central.py, ble_peripheral.py]
2024-11-12 Fixed central and peripheral BLE roles and corrected debug output
    [ble_central.py, ble_peripheral.py, main.py]
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2024-11-14 Bug fix to logging module and clean up of debug vs info messages
    [ble_central.py, ir_uart.py, log.py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]
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2024-11-18 Integrated command shell better and fixed debug output to use f-strings
    [ble_central.py, command_shell.py, eeprom.py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]
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2024-11-19 A lot of code review and fixes to the robot firmware
    [ble_peripheral.py, configuration.py, drv8825.py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]
2024-11-19 Fixes to class names PEP8 and included new class for 32-bit status flag communication
    [ble_central.py, command_shell.py, ir_uart.py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]
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2024-11-21 Fixed the library simlinks. Fixed the firmware projects. Changed code to use library classes and removed data_encode stuff
    [ble_central.py, ble_peripheral.py, command_shell.py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]
2024-11-21 Implemented some basic commands over BLE and fixed some bugs
    [ble_peripheral.py, drv8825.py, main.py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]
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2024-11-22 Fixed the velocity class to work correctly again
    [main.py, stepper.py, velocity.py]
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2024-11-22 Redesigned body, motor bays and motor mounts to fit a slimmed 24mm NEMA 17 with better clearance
    [body.scad, main.scad, motor_bay.scad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]
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2024-11-24 Redesigned wheels to allow physical axel width calibration. Changed axel width to 224mm (was 230mm) Added position markers to the bottom of the motor bays
    [motor_bay.scad, wheels.scad]
2024-11-24 Fixes for issues #55 #54 and #53
    [eyes.scad, motor_bay.scad]
2024-11-24 Fixed to body support enforcers (screw hole positions have moved)
    [body.scad]
2024-11-24 Fix for issue #56, removed 1mm from servo horn
    [servo.scad]
2024-11-24 Fix for issue #39 - added support enforcers from upper and lower stand covers
    [main.scad, stand.scad]
2024-11-24 Update to communicator scad to make PCB smaller before kicad redesign
    [case.scad, holder.scad, ircover.scad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]
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2024-11-25 Moved servo up 1 mm to clear DIN 912 screw heads. Also moved pen-up position to correct it against new servo horn position
    [pen_holder_base.scad, pen_holder_cap.scad, pen_holder_top.scad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]
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2024-11-26 Added command_uid to RobotCommand class as well as some minor bug fixes
    [ble_peripheral.py]
2024-11-30 Changed status LED functionality to make it clearer that the robot is running plus some minor bug fixes and additional docstrings
    [main.py]
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2024-12-06 Corrections to parallel code for new hardware. Added simple options class for new communicator option jumpers
    [main.py, options.py, parallel_port.py]
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2024-12-07 Added calibration commands and fixed buggy one-shot stepper motion. No way to save calibration yet.
    [diffdrive.py, main.py, metric.py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]
2024-12-07 Corrected a mistake in the wheel diameter calibration and openscad calculation Changed calibration parameters to micrometers (um) as it make better sense like that
    [wheels.scad]
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2024-12-08 Fixes for isssues #63 and #62
    [ble_central.py, led_fx.py, main.py]
2024-12-08 Improved charger case design and fixed issue #50
    [base.scad, lid.scad, light_pipe.scad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]
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2024-12-10 Added robot configuration with EEPROM load/save/reset
    [configuration.py, main.py]
2024-12-10 Fixed small bug with get-turtle-id command
    [main.py]
2024-12-11 Fixed issues #69, #67 and #66
    [calibration.scad, lid.scad, light_pipe.scad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]
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2024-12-13 Fixed pentagons so they match with the original turtle shell
    [shell2.scad]
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2024-12-13 Formed whole of the main shell, but the pentagon radii are a little too big
    [shell2.scad]
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2024-12-13 Removed old shell design and replaced it with the new one. Updated the openscad generation script
    [main.scad, shell.scad, shell2.scad]
2024-12-13 Fixed shell supports and modified motor mounts to fit new shell
    [main.scad, motor_mounts.scad, shell.scad]
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2024-12-15 fix for issue #12
    [aux_pcb_mount.stl, battery_clip.stl, battery_pack.stl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]
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2024-12-17 Fixed a bug in the robot STL generation script to generate the missing back PCB mount STL
    [aux_pcb_mount.stl, battery_clip.stl, battery_pack.stl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]
2024-12-18 Fix for issue #17
    [base.stl, charger_lid_support_enforcers.stl, connector.scad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]
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2024-12-18 Changed Micropython logging to picolog - this is to make it easier to avoid conflicts with the 'logging' module
    [ble_central.py, ble_peripheral.py, configuration.py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]
2024-12-18 Moved the eeprom class out of the library and into the robot firmware fixing issue #13
    [eeprom.py, main.py]
2024-12-18 Fixed linux vt2comms to harmonize logging with the pico firmware
    [ble_central.py, main.py]
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2024-12-19 Couple of bug fixes and a PDF for issue #11
    [eeprom.py]
2024-12-24 Refactored commands with new cartesian commands and fixed the diff_drive class to make the commands function. Also updated the Acornsoft logo extension
    [diffdrive.py, main.py]
2024-12-24 Improved cartesian code that turns and moves in the shortest direction to reach the required coordinates
    [diffdrive.py]
2024-12-27 Check-in of host code - doesn't work at the moment, but is mostly there
    [ble_central.py, ble_peripheral.py, commands_tx.py]
2024-12-27 More fixes to the BLE code. Now works except, if you pause, it crashes
    [ble_central.py, ble_peripheral.py, commands_tx.py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]
2024-12-28 Implemented first BLE commands with response. Fixed some bugs.
    [commands_rx.py, commands_tx.py, control.py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]
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2024-12-28 Minor bug fixes and improved exception handling of command reponses
    [commands_tx.py, control.py]
2024-12-28 Added a cat - yes really, a cat. Also fixed some bugs and improved the one-shot motion of the turtle
    [diffdrive.py, stepper.py]
2024-12-29 Made the commands synchronous and split command and battery testing. Fixed some bugs on the robot side to more cleanly disconnect BLE
    [ble_central.py, ble_peripheral.py, commands_tx.py]
2024-12-29 Fixed a bug in the BLE code that caused runtime errors if you connect, disconnect and then connect again
    [ble_central.py]
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2024-12-30 Fixed bug - EEPROM configuration was not read when the robot powers up initially
    [control.py]
2024-12-30 Improvements to the stepper control. Target speed and acc is now dynamically lowered if the initial values are too high. This makes one_step motion extremely unlikely.
    [diffdrive.py, stepper.py]
2024-12-30 Fix to the CLI and an improvement to the calibration spreadsheet
    [VT2_Calibration.ods]
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2024-12-30 Added arc_left and arc_right commands to draw circles. All works except the x,y,heading update is wrong
    [commands_rx.py, commands_tx.py, control.py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]
2024-12-31 Changed heading and coordinates to the correct mathematical implementation (like python turtle). Nearly all fixed apart from the arc turns
    [commands_rx.py, commands_tx.py, control.py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]
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2024-12-31 Fixed the position implementation so it maintains heading (just like logo)
    [diffdrive.py]
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2025-01-04 Some fixes to the new communicator firmware and logo extension after some quick testing
    [ble_central.py, serial_comms.py]
2025-01-04 Changed diffdrive to use um rather than mm. Fixed some bugs in the circle drawing commands (missing calibration)
    [commands_rx.py, configuration.py, diffdrive.py]
2025-01-05 Changed everything to floats and then smoothed the error in the stepper.py module. This has help accuracy a lot. Stepper.py also shows the error margin (in steps) in debug - after every move
    [diffdrive.py, stepper.py]
2025-01-05 Fix for issue #27 and some improvements to the vt2_demo app
    [diffdrive.py, stepper.py]

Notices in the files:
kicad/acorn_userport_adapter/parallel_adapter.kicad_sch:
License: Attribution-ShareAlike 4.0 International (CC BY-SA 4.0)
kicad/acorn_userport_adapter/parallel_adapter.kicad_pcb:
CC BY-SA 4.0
